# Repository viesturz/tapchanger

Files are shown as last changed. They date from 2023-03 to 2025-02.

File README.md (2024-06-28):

# Tapchanger

A nozzle Z probe + toolchanger for Voron 2.

## Features
* Off the shelf voron parts, except for bearings.
* Uses [Dragon Burner](https://github.com/chirpy2605/voron/tree/main/V0/Dragon_Burner) toolhead - can fit 6 hotends in 350 frame. [Stealthburner](https://github.com/VoronDesign/Voron-Stealthburner) and MiniStealthburner 
are an option but limited support. (Experimental version of the [Rapid Burner](https://github.com/chirpy2605/voron/tree/main/V0/Rapid_Burner) is in the works by @Marshalldog) (Experimental version for the [Xol-Toolhead](https://github.com/Armchair-Engineering/Xol-Toolhead) is in the works)
* Uses [OptoTap](https://www.google.com/search?q=optotap) probe sensor for nozzle Z probing.
* Same [rigidity](https://youtu.be/mGRXtK9F408) and probe accuracy as Tap.
* Same external printer dimensions, except for top hat.
* No servos, no wires on the shuttle, recommended to use with a Canbus toolhead board for less wires, but anything goes.

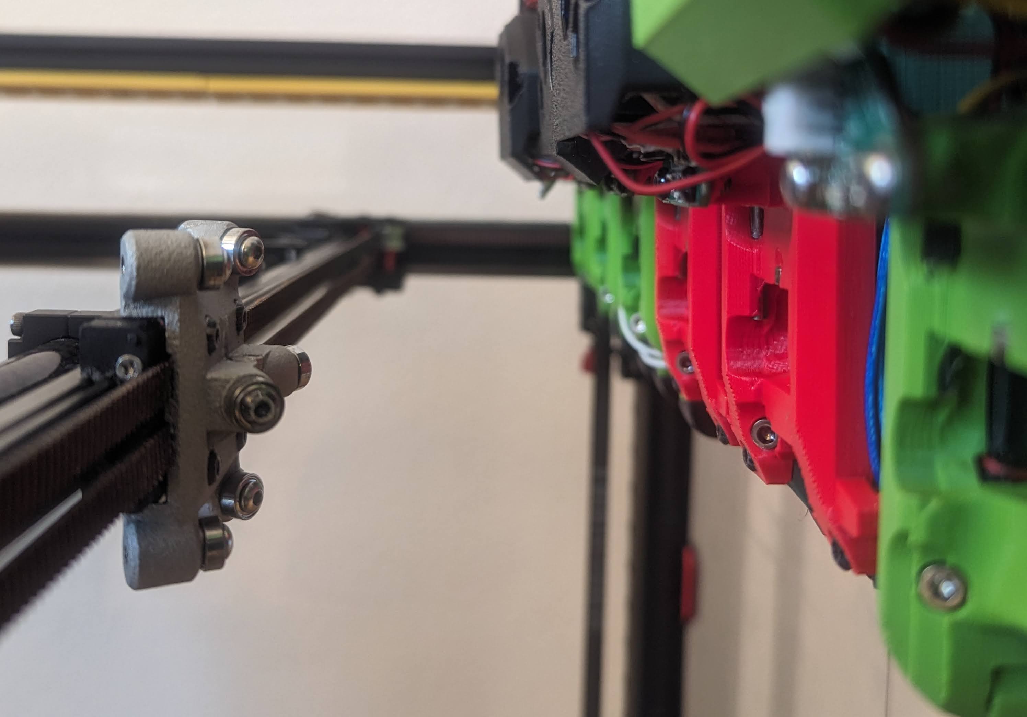
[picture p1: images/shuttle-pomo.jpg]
Shuttle

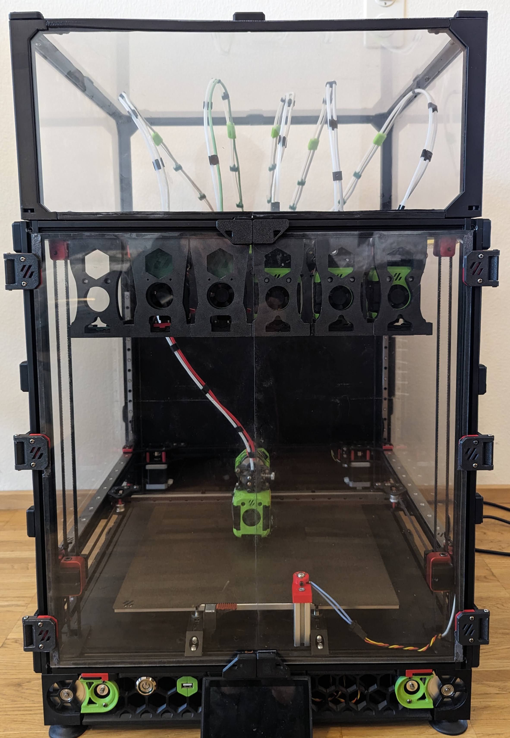
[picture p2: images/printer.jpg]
Printer
 

# Build guide

I would recommend to get a single hotend working first:

* Check the [BOM](/Tapchanger/BOM.md).
* [Print](./Print%20Guide.md) the parts.
* [Assemble](/Tapchanger/Assembly.md) it.

Multiple tools setup:
* Install [Umbilical](/Umbilical/Umbilical.md).
* Install [Docks](/Dock/Dock.md)
* Add a [TopHat](/TopHat/TopHat.md)
* Configure [Klipper](/Klipper/README.md)
* Calibrate the offsets. I'm using [this](https://github.com/viesturz/NozzleAlign)

# Community

Improvement ideas - bugs, pull requests welcome. Find me on [Voron Toolchangers Discord](https://discord.gg/xmDWrYGwVJ), or file bugs here.

See Tapchanger [youtube channel](https://www.youtube.com/playlist?list=PLqU7kX5nUJDRDw5z0NLwJ22OkV6fbjnSW).

# Credits

- Basic models from [Voron Stealthburner](https://github.com/VoronDesign/Voron-Stealthburner) and [Voron 0](https://github.com/VoronDesign/Voron-0).
- Mini SB Orbiter cowling form [mozartlovescats](https://www.printables.com/model/366337-voron-02-orbiter-20-trianglelab-chc-mini-stealthbu).
- Mini SB LGX lite cowling form [MC](https://www.printables.com/model/395933-voron-02-mini-stealthburner-remix-for-lgx-light-ex/files).
- Dragon Burner from [chirpy2605](https://github.com/chirpy2605/voron/tree/main/V0/Dragon_Burner).
- HGX gears extruder derived from [nhchiu's ProtoXtruder](https://github.com/nhchiu/VoronMods/tree/main/Extruders/ProtoXtruder)

# How does this work?

It's essentially an oversized linear rail, that supports only ~4 mm of travel. The steel rail is replaced by bearings riding on rods.

In addition, it's a kinematic mount, meaning that it's self aligning and there is no play even if the parts are not aligned precisely.

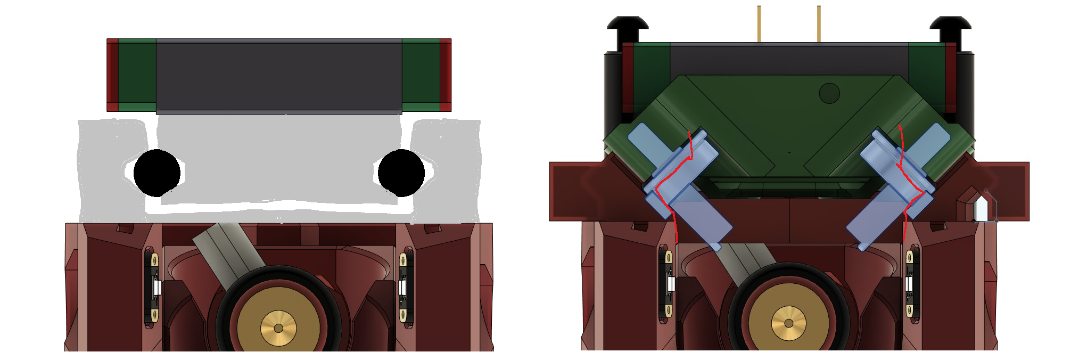
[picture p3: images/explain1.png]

Shuttle

# Revision history:

## V4.3
Dragon burner printability, ease of assembly tweaks:
* Two piece mount plate with less supports needed
* Better access to the heatset inserts
* Slightly larger sensor screw holes to better work with polycarbonate
* Will need to reprint the cowling as well, slight changes there

## V4.2
Small tweaks across the board:
* Dragon toolhead mount plate 1mm thicker - no interferance with fans and 8mm tensioning screws do not stick out
* Fix shuttle mounting plate misalignment, thanks [vikwin](https://github.com/vikwin) for spotting
* Alternative version for the PFTE tube holder at the side
* Dock for RapidBurner
* Extras
  * Better ventilated EBB36 shield 
  * Improved strain relief for HGX + DragonBurner
  * More Stepper gear distance adjustability for HGX + DragonBurner.

Dragon burner toolhead exploded view: 

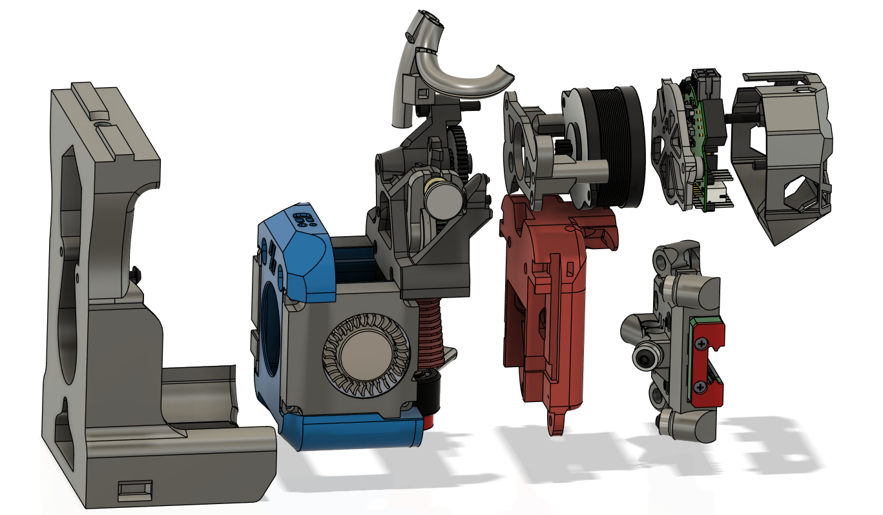
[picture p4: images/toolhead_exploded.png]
Exploded


## V4.1
HGX gears + Dragon + EBB36 [optimized toolhead](/Tapchanger/STL/Toolheads/DragonBurner/HGX%20Gears/):

* 17 mm shorter filament path
* 17 grams lighter than stock, only 2 screws
* Integrated harness strain relief
* Integrated EBB36 mount & shield
* Bambu & Revo adapters only for now
* There will be some supports to remove.

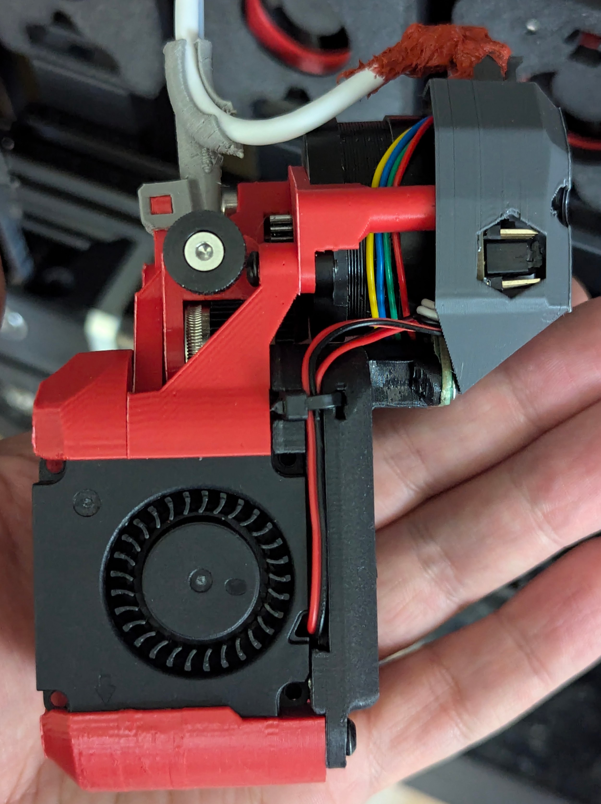
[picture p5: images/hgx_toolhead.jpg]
HGX gears toolhead


## V4.0
[Liftbar dock](/Dock/Liftbar/Liftbar.md)

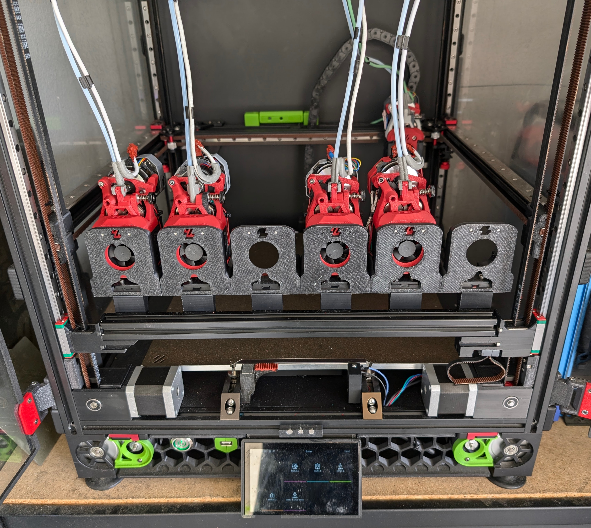
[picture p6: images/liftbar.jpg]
Liftbar


Other minor DragonBurner changes:
* More clearance around the hookon slot.
* More room around the cooling fans, to avoid cracking the cowling when tightening the bottom screws.
* More sturdy dock.

## V3.2
Introduces support for the Experimental Rapid Burner Toolhead by @Marshalldog.

## V3.1
End of year update, lots of small printability, clearance, etc updates. 
This is a stable version.

* Migrated to Dragon V8 hotend.
* More clearance around the OptoTap sensor.
* Tuning of the tension screw angles to minimize the docking resistance.
* More clearance for big block hotends.
* Hook-on dock is now the recommended for DragonBurner.

## V3.0

Further improvements to DragonBurner toolhead and dock.
The screw head locking mechanism is back.
Configuration updated, with better dock pathing.

The Dragon Burner toolhead is now the default. Let me know if you would like to see backports.

## V2.9

Improved DragonBurner toolhead and dock, adding bottom mounting screws for better stability.
Needs the modified cowling now.

## V2.8

# Added Tophat and Ubmilical, it's now a Printer!

Printer 

## V2.5

* Added top mounted dock. see updated Dock folder.
* Slight tweaks square rods mounting plate for easier fit.

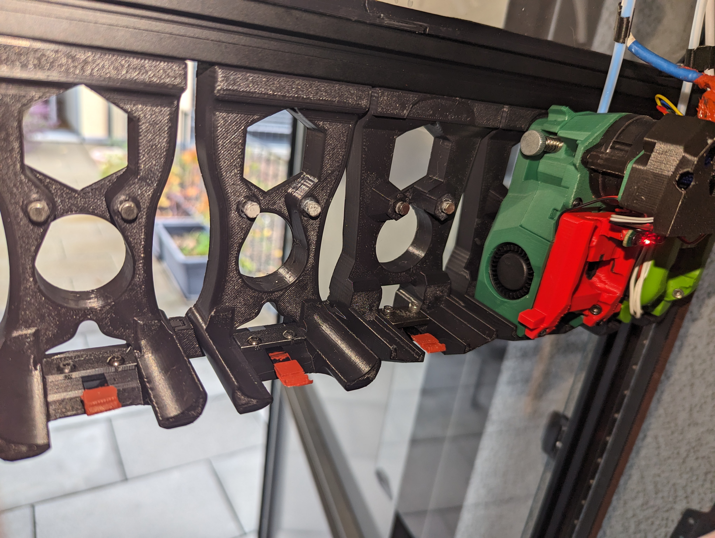
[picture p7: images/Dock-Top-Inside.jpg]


## V2.3 - Nozzle pads upgraded to springsteel ones, no more melting.

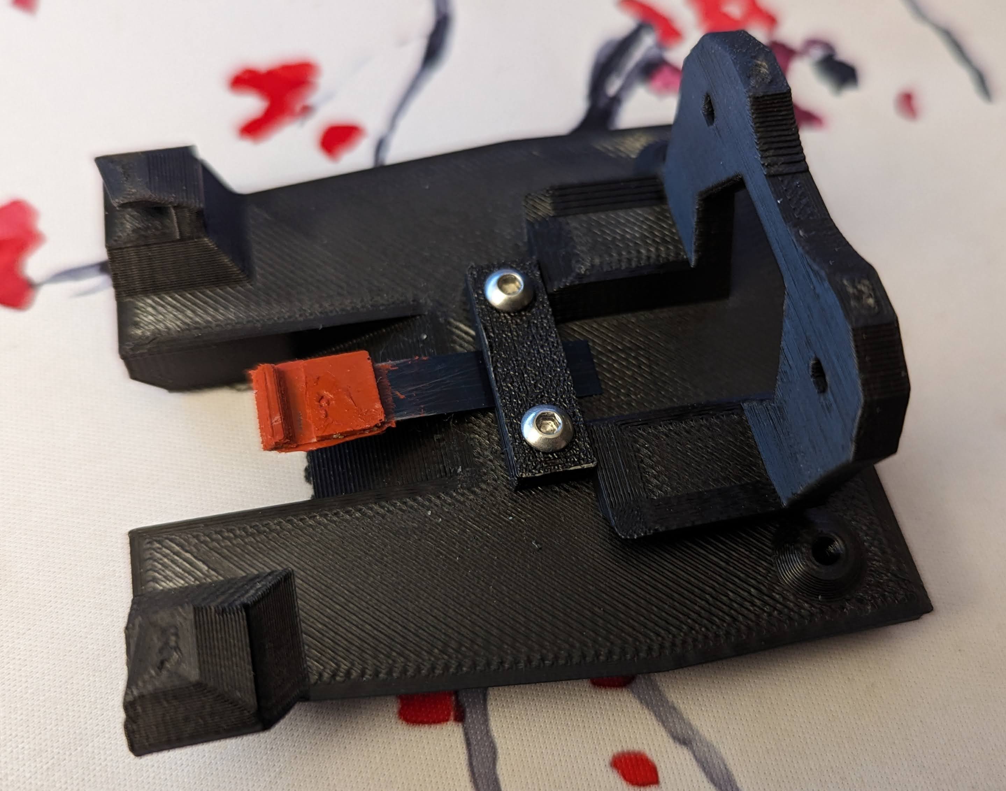
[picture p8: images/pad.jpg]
Pads


## V2.2 - Square rods version added.

Option to use square rods for better contact surface for the bearings.  Shares the shuttle and bearings with rods.

There are now total of 3 versions:
 - Plates - bigger bearings, more work to make the plates and assemble. The rolling surface is not great. Very rigid.
 - Rods - smaller bearings, easiest to assemble, but more flex.
 - Square rods - middle ground between plates and rods, the rigidity testing was done with this.

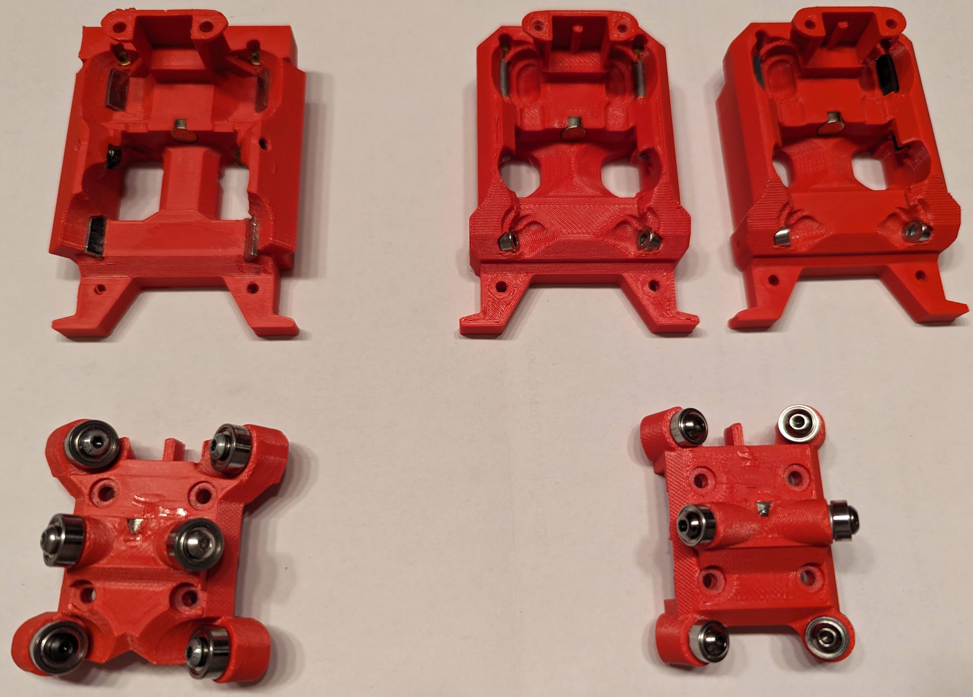
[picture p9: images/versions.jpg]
Versions


## V2.1 - Rods fixes.

Various fixes to refine the rods version. Ready for general testing.

## V2 - Rods version added.

A new experimental version using 3mm rods. See -rods files. Shuttle and mount plates changed, the rest is same.

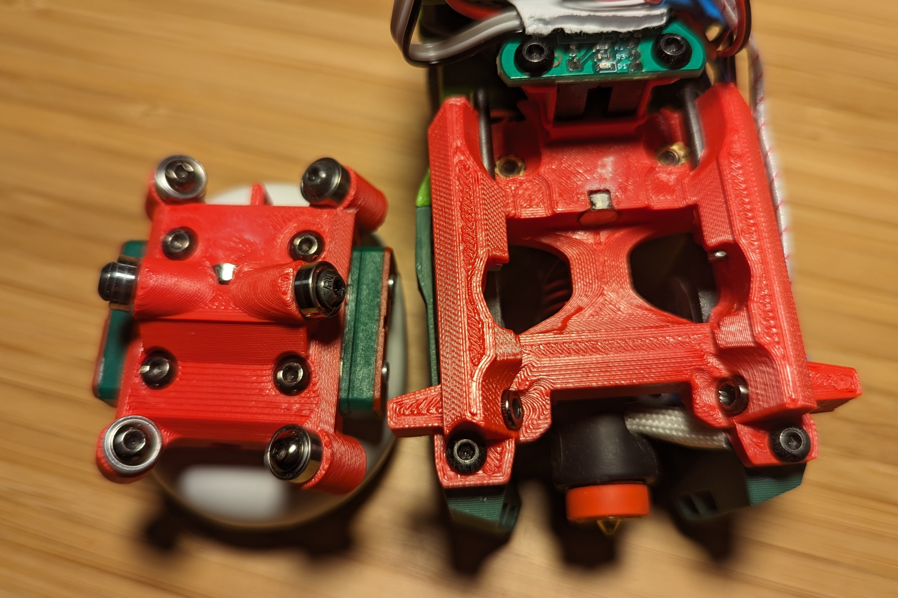
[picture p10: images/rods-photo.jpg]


- Easier to assemble
- Tension adjustment screws easily available
- Runs smoother
- Using smaller 3x8x3 bearings - saves 5 grams and even more rigid.
- Even load distribution between the bearings by adjusting the angles to 26 and 64 degrees.

## V1.1 - Verified and cleaned up.

- Minor model tweaks for better fit and printability.

## V1 - This should work

- Redesigned and optimized - not compatible with V0
- Significanly more rigid
- Supports both Mini and full size Stealthburner

## V0 - Initial drop
 
 - It can print and looks reasonably rigid
 - ~10 Tool chnages so far
 - Initial dock, that looks okay for the job

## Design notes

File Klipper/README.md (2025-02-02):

# Klipper setup

## Overview

TapChanger is primarily a hardware project. The config here is just the setup I'm using.
Which should be a reasonable starting point.

I'm working to upstream the changes in klipper where reasonable.

## Installing

- Install [toolchanger extension](https://github.com/viesturz/klipper-toolchanger/).
- Use the [config examples](https://github.com/viesturz/klipper-toolchanger/tree/main/examples) to setup your Klipper config.

## Prusa slicer config

I'm using the following custom Gcode.

**Start Gcode** - all must be a single line
```
PRINT_START  TOOL_TEMP={first_layer_temperature[initial_tool]} {if is_extruder_used[0]}T0_TEMP={first_layer_temperature[0]}{endif} {if is_extruder_used[1]}T1_TEMP={first_layer_temperature[1]}{endif} {if is_extruder_used[2]}T2_TEMP={first_layer_temperature[2]}{endif} {if is_extruder_used[3]}T3_TEMP={first_layer_temperature[3]}{endif} {if is_extruder_used[4]}T4_TEMP={first_layer_temperature[4]}{endif} {if is_extruder_used[5]}T5_TEMP={first_layer_temperature[5]}{endif}  BED_TEMP=[first_layer_bed_temperature] TOOL=[initial_tool]
```

**Tool change Gcode**
```
M104 S{temperature[next_extruder]} T[next_extruder] ; set new tool temperature so it can start heating while changing
```

## Optional - Z homing with any toolhead.

The included config has a rather elaborate setup that allows Z homing with any toolhaed. This avoids the need to ensure that toolhead 0 is mounted before homing.

The tool changing needs reasonably repeatable gantry Z position, since Tap homes to nozzle possition, it will be different for each toolhead.

So this is a bit more complicated than yor typical setup:

  - Printer Z=0 - is tool independant, all toolchange moves happen in this space.
  - Tool probe trigger Z offset - distance betwen nozzle touching the bed and probe triggering - is tool specific, but nozzle independant. Specified in tool_probe.z_offset.
  - Tool Z offset - is tool and nozzle specific. Specified in tool.offset.

When **homing** the Z=0 is determined from probe tigger location - probe trigger offset - tool Z offset.
For Tool 0 that is the same as normal Tap homing. For other tools the extra tool offset is substracted.
Klipper unfortinately assumes that the Z=0 is a fixed distance from the endstop trigger location, so there are some tricks in homing.cfg to adjust this in post.

When **printing**, the Gcode offset is = tool Z offset.

When **changing tools**, Gcode offset = 0.

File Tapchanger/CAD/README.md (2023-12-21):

The holes are not present in the CAD. Please use the provided hole models to cut either square or round holes.

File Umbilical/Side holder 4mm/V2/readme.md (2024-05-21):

Side PTFE tube holder with individual locking nuts.

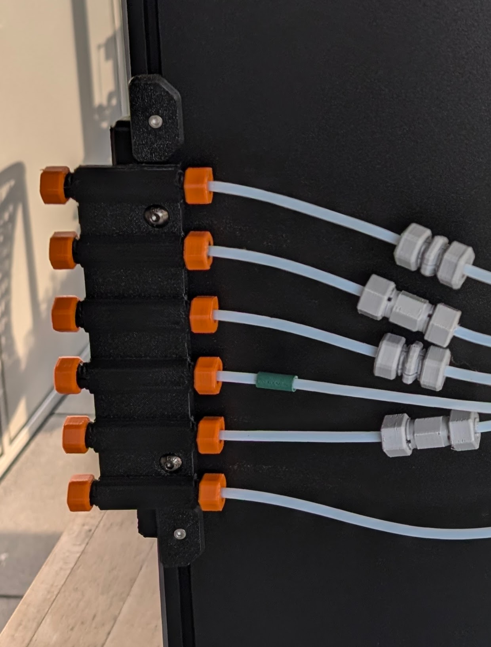
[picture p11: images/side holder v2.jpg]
Preview


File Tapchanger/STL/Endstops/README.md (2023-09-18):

# Endstops

I recommend sensorless XY. 

# X endstop on Y axis

Use `HallSensor.stl` - it is a copy of Tap switch/magnet mount adapted for the shuttle.

# X endstop on Gantry

Very prototypy, moves the X endstop to the gantry, removing wiring to Y axis.

Use `X Endstop Lever.stl`.

It's very specific for Chaoticlabs motor mounts and some Y endstop PCB I had laying around.

Preview
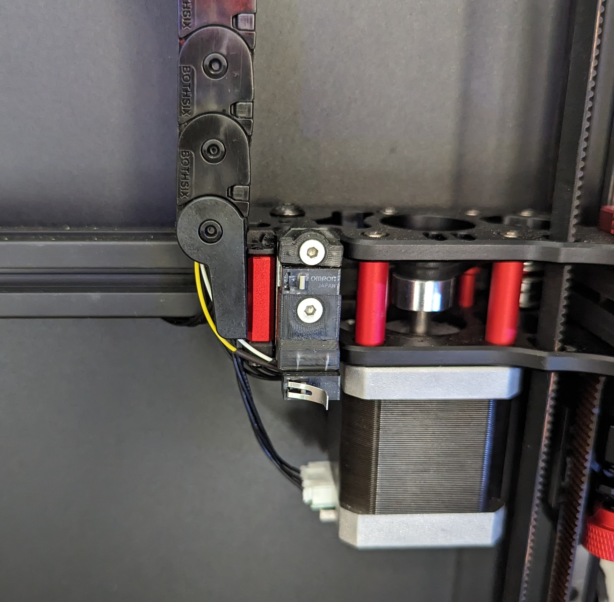
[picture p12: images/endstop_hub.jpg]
Preview


Ping me if you happen to make a better solution.

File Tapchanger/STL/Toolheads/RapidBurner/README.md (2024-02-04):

### Rapid Burner Toolhead implementation is experimental and currently under testing by @Marshalldog.
### Use the parts from the Dragon Burner (except the cowl).
# This is EXPERIMENTAL. If you have issues, please post them on the tapchanger discord ASAP!

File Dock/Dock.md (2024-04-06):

# The dock

The dock comes in 3 versions - cross beam mounted, top mounted or on rails.

| Top mounted  | Cross beam | Liftbar | 
| --- | --- |  --- |
| * Can be installed in existing frame<br> * Good clearance |  * Supports Full sized Stealthburner <br>* Extra docking latch | * Complex to build <br> * Best clearance <br>* Slightly faster changes<br>* Can install on Trident |
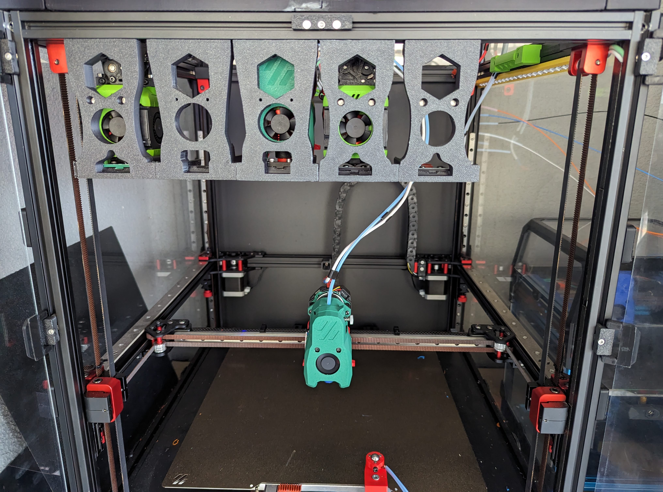
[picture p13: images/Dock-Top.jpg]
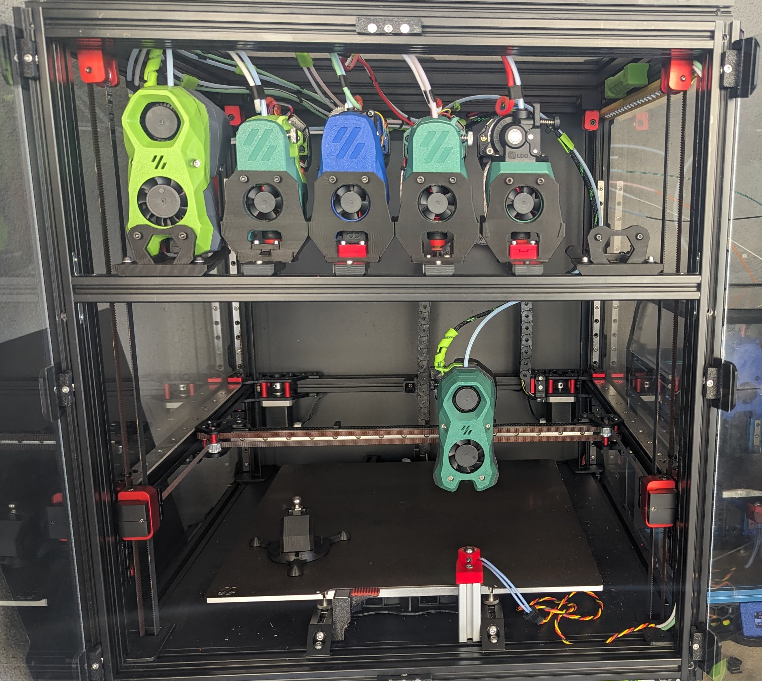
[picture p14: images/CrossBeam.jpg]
|  |   |  Preview  | 
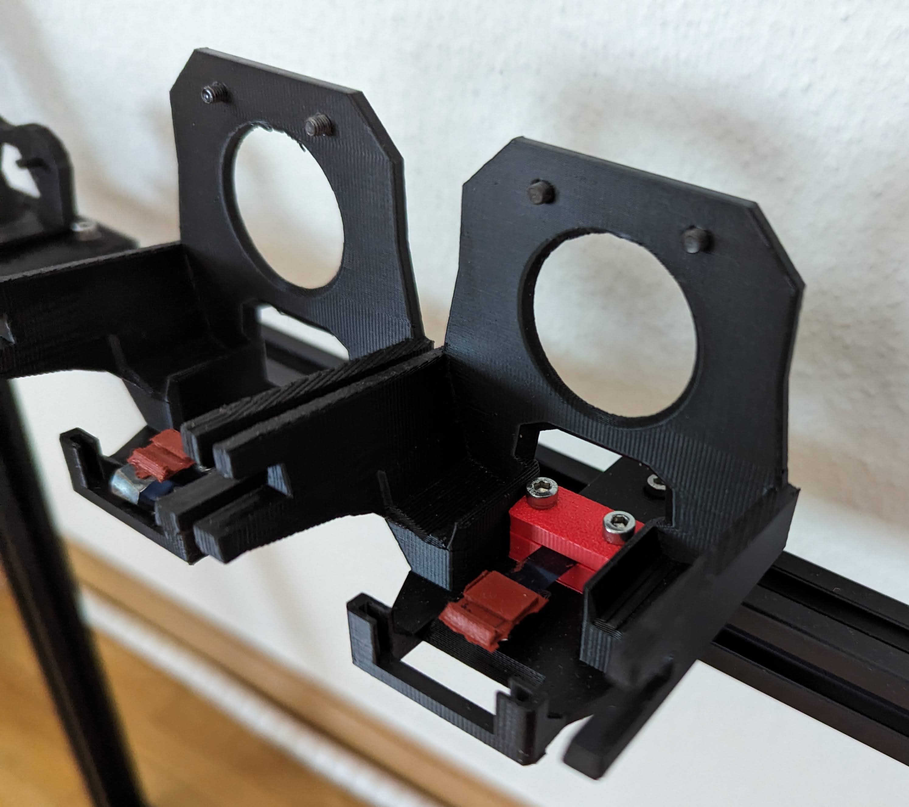
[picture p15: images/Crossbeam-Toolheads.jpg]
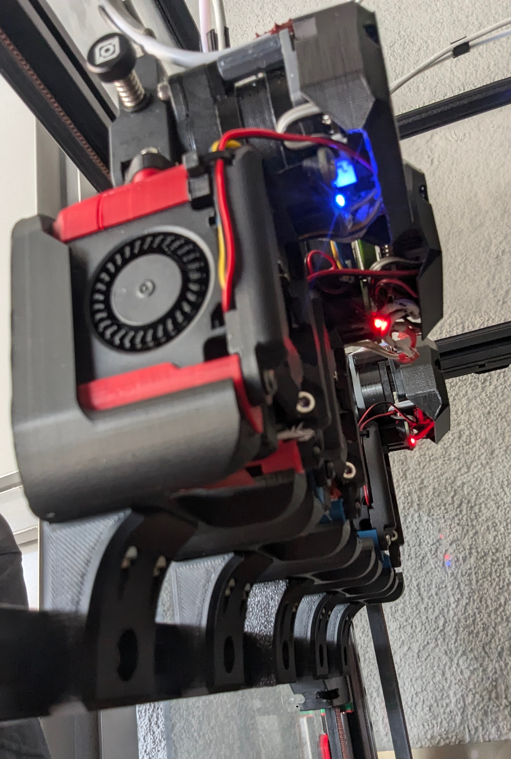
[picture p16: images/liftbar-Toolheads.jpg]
| Preview |  |  |

# Liftbar dock 

See [Liftbar instructions](./Liftbar/Liftbar.md)

# Other docks BOM

 - High temp silicone for the nozzle pad
 - 35 mm of 7x0.1mm springsteel, salvageable from 1m tape measure.  
 - some M3 screws and heatset inserts
 - *retnetion hardware* - see below

# Toolhead retention

There are 2 versions of retentiom mechanism, this will likely converge as I get more relibility data

## Screw head hook

Dragon burner uses this method.
The toolhead hooks on to the M3 scew heads. Just need 2x m3x10 butthonhead screws.

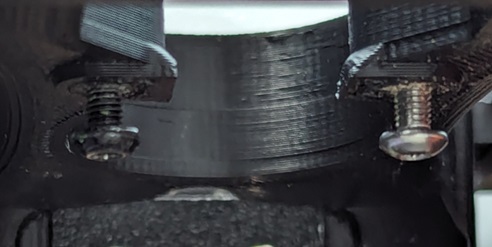
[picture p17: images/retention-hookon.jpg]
Cross beam retention


## Bottom pin + magnet to toolhead screws.

Stealthburner and mini stelathburner on cross beam uses this approach.
It relies on a bottom pin as the main retention mechanism and the magnet is just to prevent it rattling around.

You will need:
  - 2x 5x2mm round magnets
  - 2x m3 x 10 steeel screws in the dock - steel (magnetic)
  - the screws in toolhead also need to be seel to stick to the magnets

Drop the magnets on the screw heads in the toolhead. They will stay there on their own, no glue required.

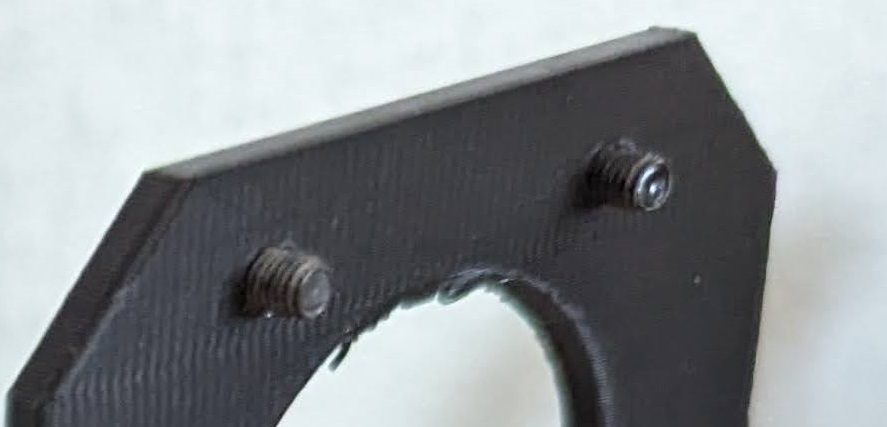
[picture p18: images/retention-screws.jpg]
Cross beam retention


# Cross Beam Frame BOM

Essentially you need to build this. The exact dimensions depend on your printer size.

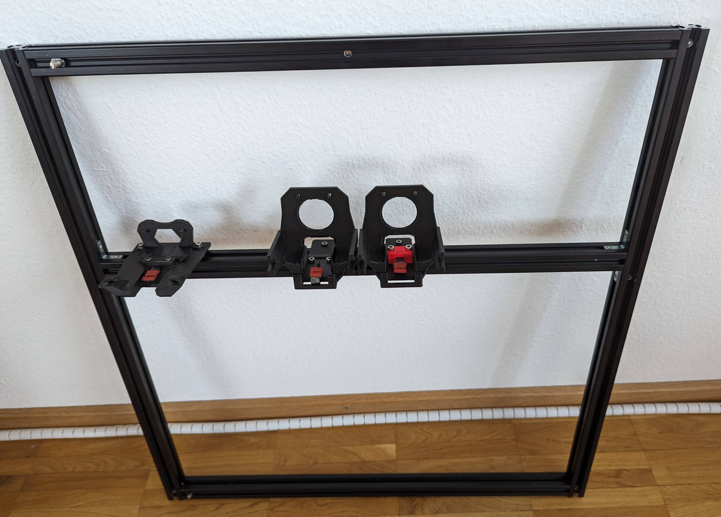
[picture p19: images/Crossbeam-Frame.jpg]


# Nozzle pad

Print the nozzle pad mold. Put on some mold release, just rubbing with a birthday candle works well. 

Cut a 35mm piece of springsteel and mold the silicone pad on one end.
The mount is designed to accomodate fror the springteel curve, place it so that it curves downwards.

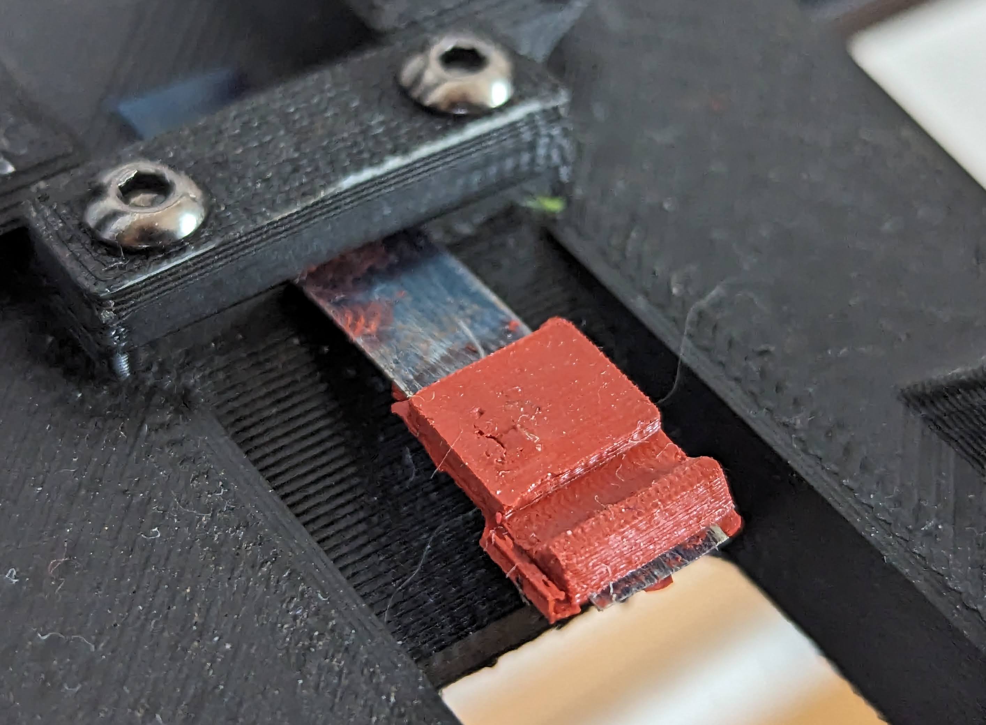
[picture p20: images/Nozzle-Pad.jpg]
Pad


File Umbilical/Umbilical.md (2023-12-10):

# Umbilical

The wiring system from the main board to all the toolheads.

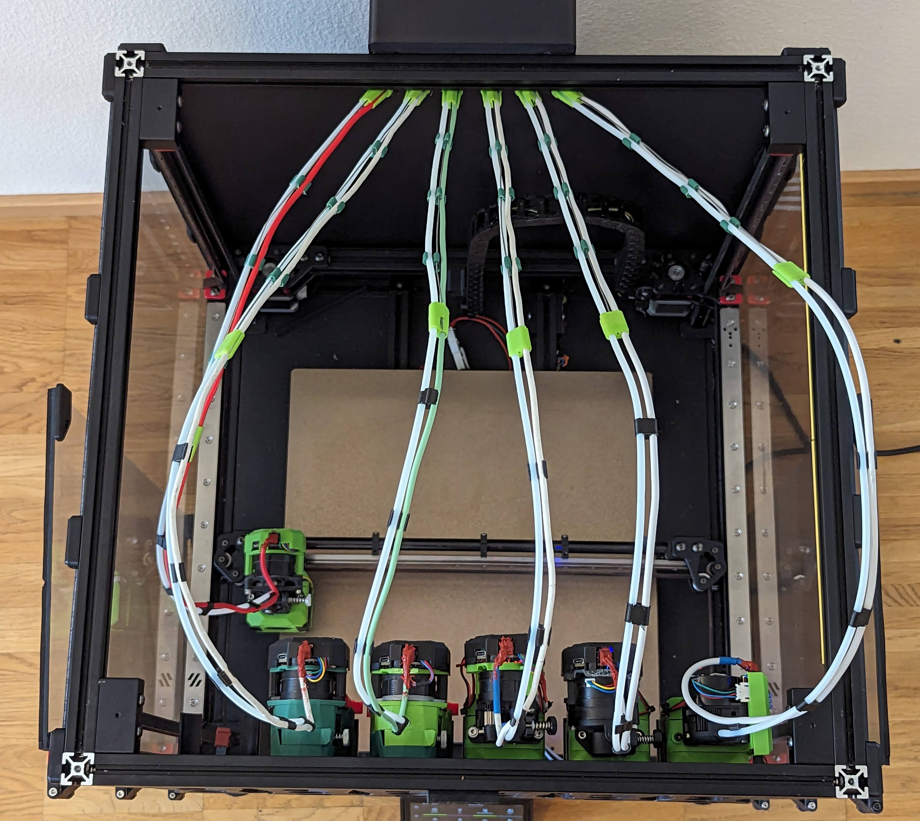
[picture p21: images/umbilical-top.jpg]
Preview


# BOM (per toolhead)

All lengths are for a 350mm bed build. Shorten accordingly for smaller sizes.

* Some TPU filament, I'm using 82a hardness.
* 34cm 1mm piano steel wire
* 1m USB cable, capable of 5amps
* silicone (high temp or normal)
* 130cm PTFE tube 4mm OD, 3mm ID
* Some m3 and m5 scews and heat set inserts

# Assembly

## Backing plate

Mount the back plate at the back of the rail, it replaces the air filter.
Route the canbus wires and 24v to it. They fit will in the extrusion slot. Remember to use appropraite gauge, for all 6 toolheads it can draw 20+ amps, and more if you go for Rapido for some reason.

I'm currently using Wagos to connect all the wires, but see the electronics folder for a custom PCB board.

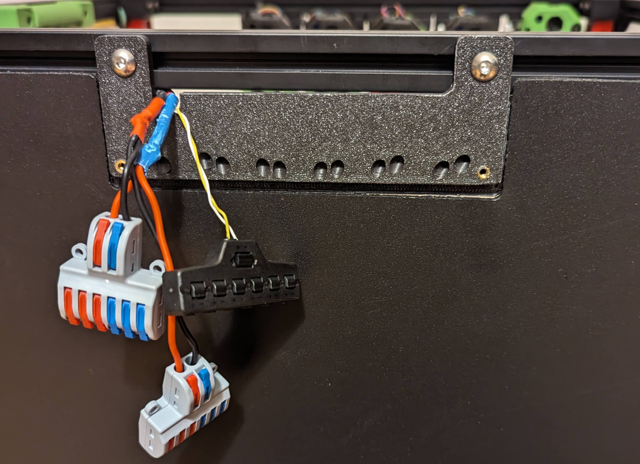
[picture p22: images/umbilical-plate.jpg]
Plate


## Prep the USB cable

Cut both connectors off, and solder/crimp on the hotend board connector. Then **fill it up with silicone**, this is high vibration connection, I had constant connection issues without this. 

Leave the other end alone for now, it will make it easier to thread through the backing plate.

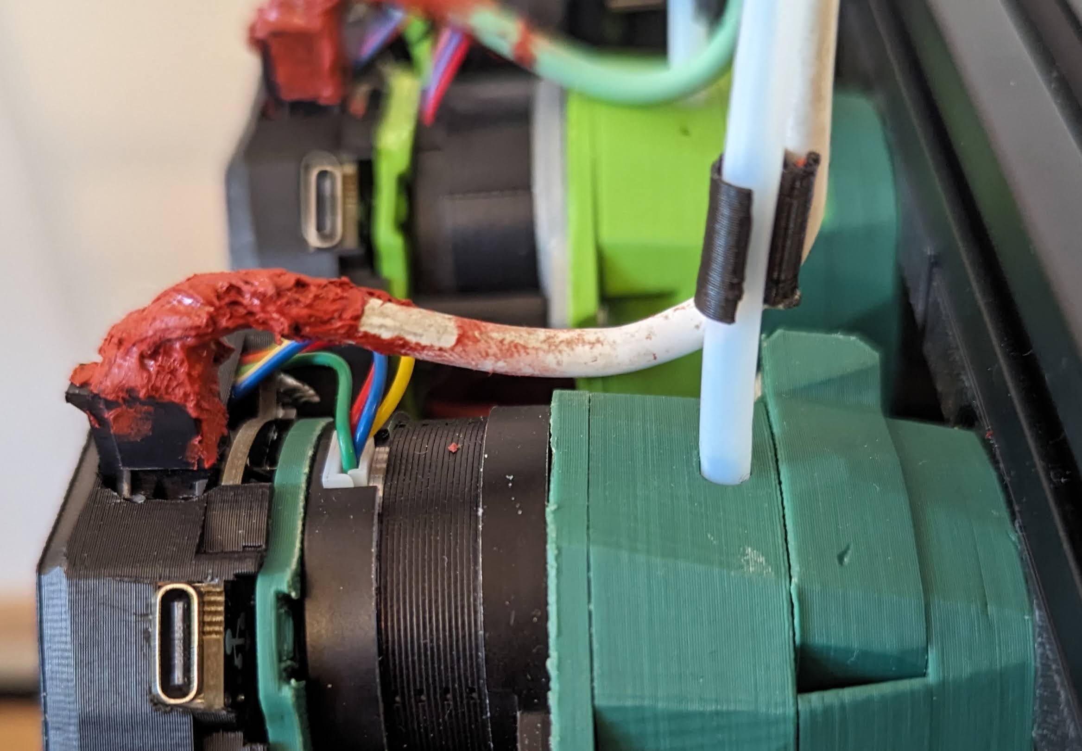
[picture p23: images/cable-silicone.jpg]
Toolhead connector


## Prep the piano wire

Cut the piano wire to length, straighten it out (holding with pliers and lightly bending works well). And fold a square hook at one end, you will need that to secure in the TPU plug.

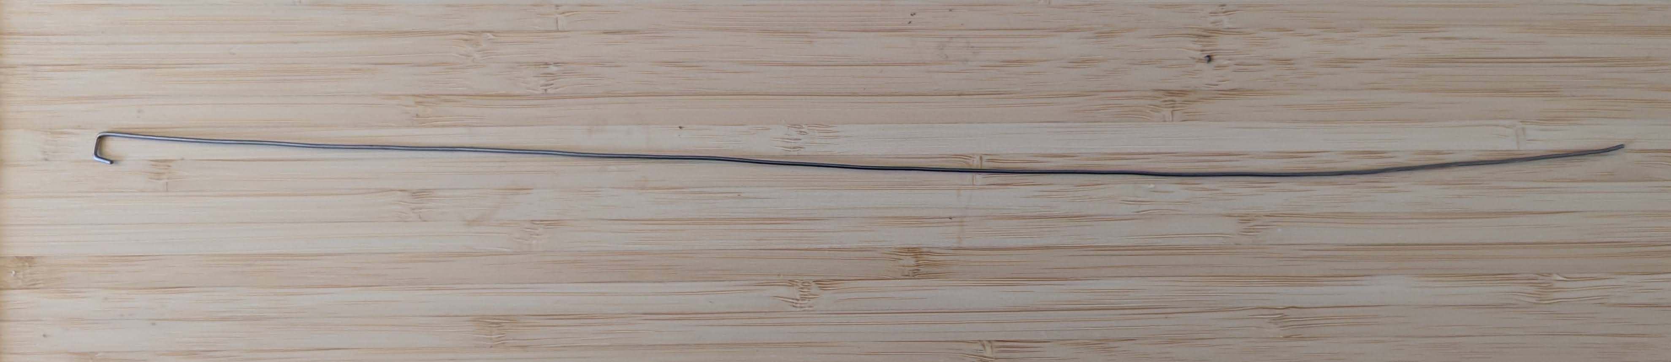
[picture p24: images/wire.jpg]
Wire


## Assemble the umbilical

Attach the both ends to the wire and put 3 wire clips in the middle. **Mind the orientation** - USB cable goes on the right and PFTE tube on the left side.
Both the clips and the hub are designed with tube on the left. The hole sizes are different so it should be obvious that something is off.

Leave around 40 cm of the tube and 45 cm of the usb cable from end of wire to the toolhead. You will be able to adjust it later.

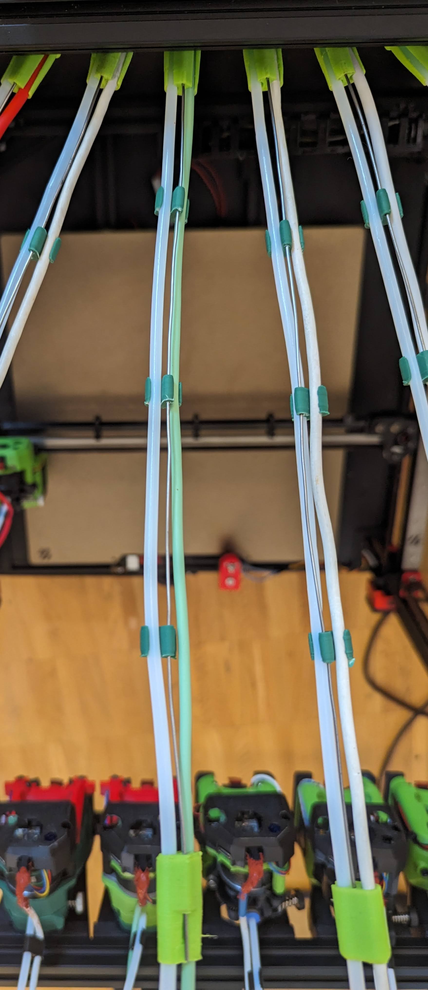
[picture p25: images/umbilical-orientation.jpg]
Umbilical


## Install

Plug the umbilical in a slot, it's a tight fit but should go in with some pressure applied. Attach the toolead.

Now move the toolhead around the print area, make sure the cable is long enough to reach every corner. Adjust the length as needed.

It should be roughly like this:

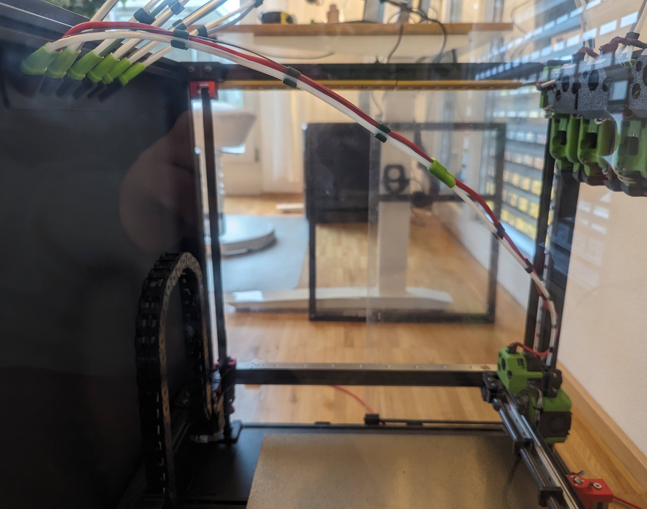
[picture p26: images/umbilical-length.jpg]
Umbilical length


## Connecting

Now you can cut the USB cables to length, strip and connect them.

See [Canbus](./canbus_wiring.md) on how to wire it all together.

**Before powering on**, verify there are no shorts and the Canbus lines have 60 Ohm between them.

## Filament routing 

Attach the tube holder to the side and route all the tubes through.
Mine where cut too short, so I had to improvise.

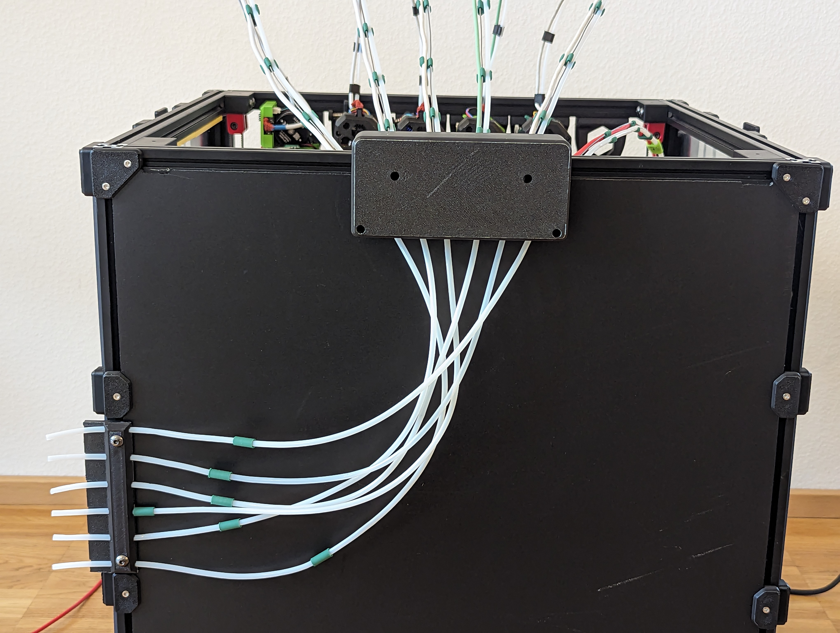
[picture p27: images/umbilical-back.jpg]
Umbilical back


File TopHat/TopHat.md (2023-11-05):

# Tophat to encose the umbilicals.

Adds a 20cm extra clearance for umbilicals. Reuses the top plate.

Theese are some big pieces to print from ABS:

- the **beams are 0.5% longer** and have bigger screw holes and support 0.5-1.5% shrinkage
- add mouse ears or there is high chance the beams will peel off

It just sits on top of the frame with alignment pins dropping down into the extrusion slots

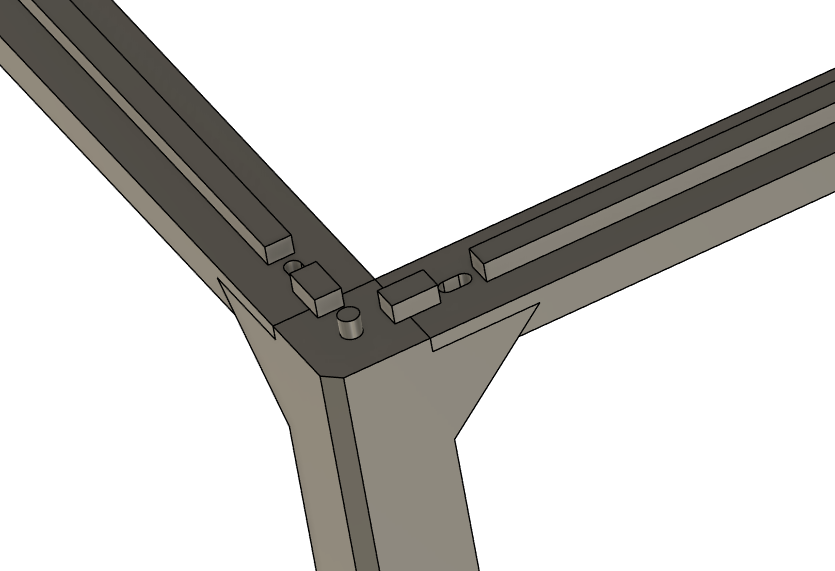
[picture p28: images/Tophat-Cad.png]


# BOM

* ~600g of filament
* 4x 200x477 acrylic plates, 3mm thickness
* 1mm sponge tape
* some M3 screws and heat set inserts

# Preview

Of an older version.
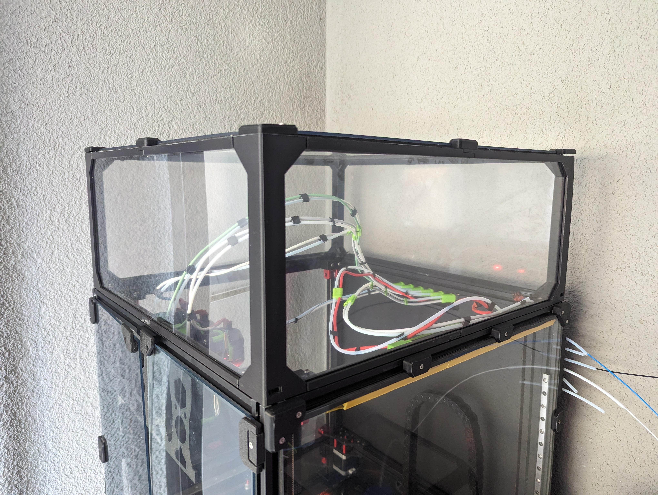
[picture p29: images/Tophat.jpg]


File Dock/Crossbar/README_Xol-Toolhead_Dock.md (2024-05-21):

# Tapchanger-Rods Xol-Toolhead (Experimental)
by [MikeYankeeOscarBeta](https://github.com/MikeYankeeOscarBeta/tapchanger) (VoronDesign Discord: #MikeyMike V2.5796, Voron Toolchangers Discord: MikeyMike - Github: [MikeYankeeOscarBeta](https://github.com/MikeYankeeOscarBeta/tapchanger))

### This is EXPERIMENTAL If you have issues, please post them on the tapchanger discord ASAP!

## Description
Tapchanger parts compatible with Xol-Toolhead (Experimental)

Based on Tapchanger StealthBurner Parts.

For crossbar (horizontal 2020 aluminium extrusion in front of printer) only!

Designed to be compatible with all Xol-Toolhead versions as of 2024-01-19.
(However only Revo Voron and Rapido 2 UHF has been tested)

#### NB! Tapchanger-Rods Xol-Toolhead dock has it's own docking tool-path. Remember to change to 'rods_xol' in your toolhead config.
In case you don't already have it from the tapchanger example config toolchanger.cfg , here's the docking tool-path:
```
params_rods_xol_path: [{'y':59, 'z':17.5},{'y':5, 'z':17.5},{'y':5, 'z':0.2},{'y':0.5, 'z':0.1},{'z':0, 'y':0, 'f':0.5},{'z':-5, 'y':0},{'z':-6, 'y':3},{'z':-8, 'y':7},{'z':-10, 'y':16}]
```

#### NB! only compatible with tapchanger rods version as of 2024-01-19

Example:
```
[tool T0]
tool_number: 0
extruder: extruder
params_type = 'rods_xol'
fan: multi_fan T0_partfan
gcode_x_offset: 0
gcode_y_offset: 0
gcode_z_offset: 0
```

## BOM:
| Part | Amount | Description |
|---|---|---|
| 6x3 magnets | 4 | N35 to N52 (N52 recommended) |
| springsteel plate | 1 | max 10mm wide, max 1mm thick, with M4 hole (I used blades from a [feeler gauge](https://www.biltema.no/en-no/car---mc/car-tools/engine-tools/spark-plug-tools/feeler-gauge-mminches-2000028588) ) |
| M4 screw | 1 | Maximum 6.3mm wide screw head |
| M3x14mm BHCS or SHCS screw  | 2 | Any M3 screw will work |
| M3 T-slot nut | 2 | Any M3 2020 T-Slot Nut will work (recommend springnuts) |

## Assembly
- Print
    - dock
    - maglock faceplate
    - tapchanger-rods xol-base
    - tapchanger-rods shuttle (if you haven't already)
- Push and glue in magnets
- Insert springsteel plate into slot in the Dock
- Cut and bend springsteel plate to fit your toolhead
- (optional) apply/mold silicone to the springsteel plate
- Fix the springsteel plate in place with the m4 screw
- Screw it onto the 2020 aluminium extrusion

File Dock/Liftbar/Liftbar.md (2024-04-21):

# Liftbar dock

A motorized crossbar - compatible with Trident and V2.

For up to 3 toolheads (2 docked), a single motor is sufficient. For more, I recommend two motors.

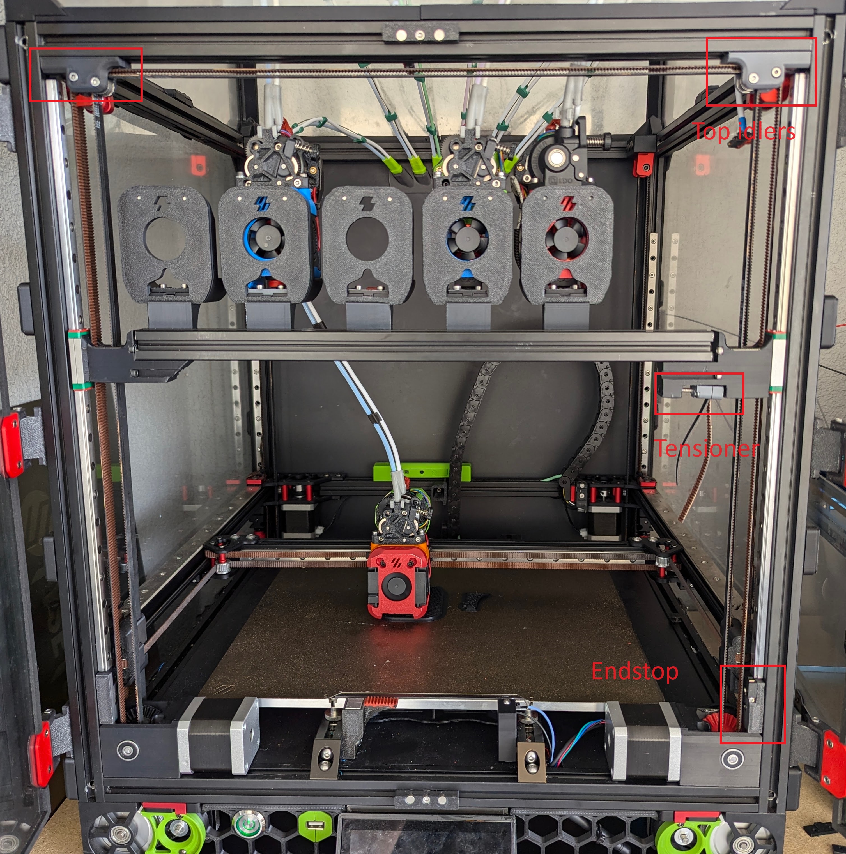
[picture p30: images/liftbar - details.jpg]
Details image


## BOM
2020 Extrusion:
 -  279mm long for 250mm build
 -  329mm long for 300mm build
 -  379mm long for 350mm build

XY Idlers:
 - 2x 20mm 5mm shaft
 - 4x heatset inserts
 - 4x 8mm m3 screw
 - existing pulleys

Common:
- Omron d2f endstop switch
- ~4m 6mm GT2 belt (for 350 size)
- m3 bolts, heatset inserts, nuts
- 8x 8mm m4 bolts, t-nuts
- 8x F623RS flanged bearings (voron 0 spec)

Voron 2.4:
- 2x MGN9H rails, same length as your Z rails

Voron Trident: 
- 2x  MGN9H rails, 210mm+

For Single motor:
- nema 17 motor
- 36mm 5mm shaft
- 2x 625 bearing (voron 2 spec)
- 20T GT2 idler
- 20T GT2 pulley
- 2x 5x1mm washers

For dual motor:
- 2x nema 17 motor
- 2x 36mm 5mm shaft
- 4x 625 bearing (voron 2 spec)
- 2x 20T GT2 pulley
- 4x 5x1mm washers

## Assembly

* Assemble and replace the the XY idlers
* Install the Top idlers
* Install the linear rails, make sure they clear the XY idlers
* Install endstop
* Assemble and connect the gearboxes
* Assemble the gantry
* Install the belt
* Adjust the belt so that the gantry is ~horizontal
* Tension the belt
* Test the lifbar movement

Work in progress...

### Gearbox

The assembly sequence is a bit tricky.

* First mount the gears - small on the stepper axis and large on the pulley. Use the grubscrews in reverse to tighten the large gear. The small gear is just friction fit.
* Then install the m3 screws for the motor, do not mount the motor yet.
* Then press fit in the rear bearing, this needs quite some force, use a rod or hex wrench through the front hole to push it in.
* Install the Left side M4 screw, but *not* the right one.
* Install the big gear, this is a bit tricky:
  * Push in the shaft through the bearing from back, have it extend 1mm inside.
  * Place the washer on the shaft
  * Push the gear assembly down from above, it's a right fit, but should go in without much force.
  * Push the shaft all the way through
  * Add the second washer and bearing.
* Install the motor, test if the gears mesh smoothly
* Install the remaing 2 M4 screws.

Cross cut vs Trident leadscrew:

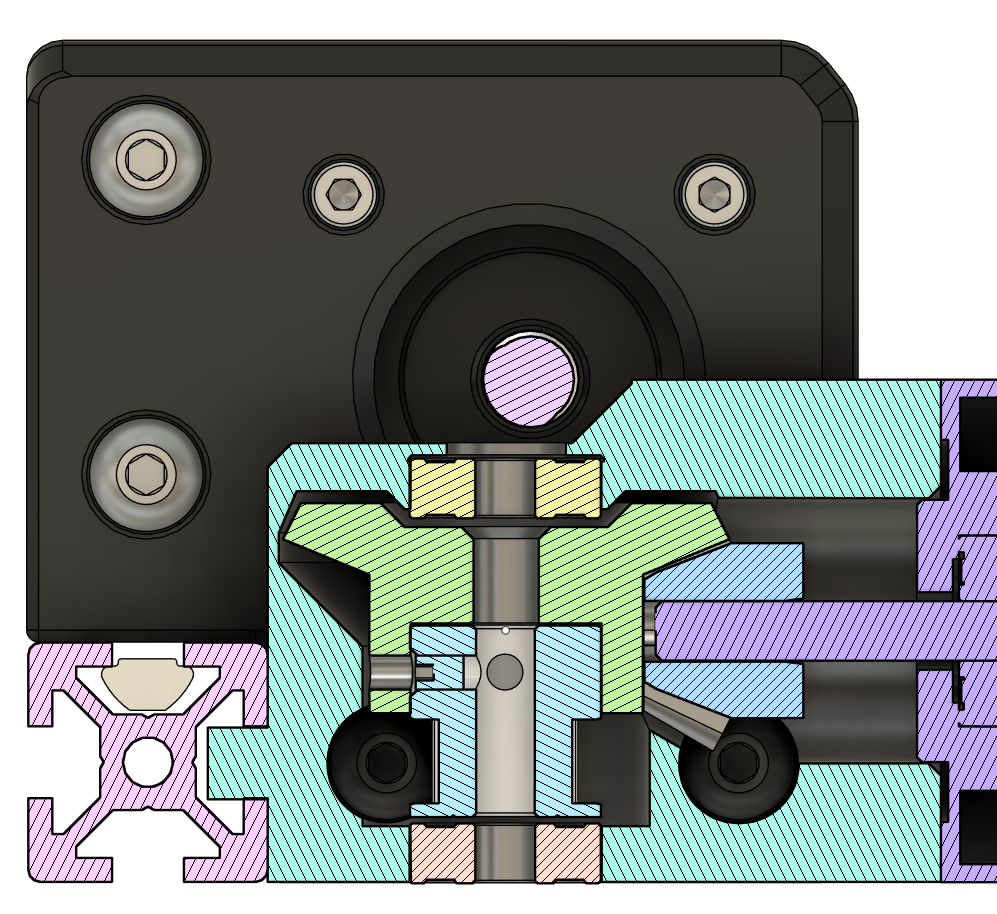
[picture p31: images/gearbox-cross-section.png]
Gearbox 0


Top down, test fitting the Motor, remove the motor to install the large gear.
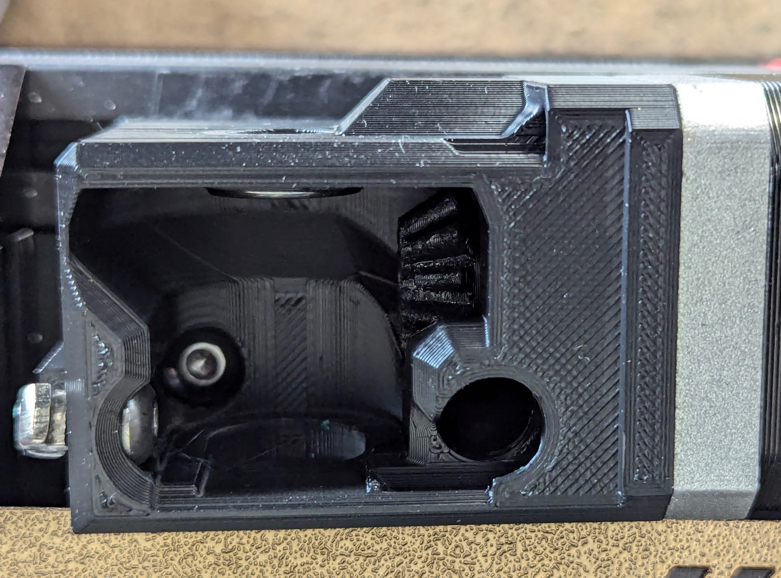
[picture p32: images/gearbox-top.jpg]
Gearbox 1


Finished, ready to be mounted:

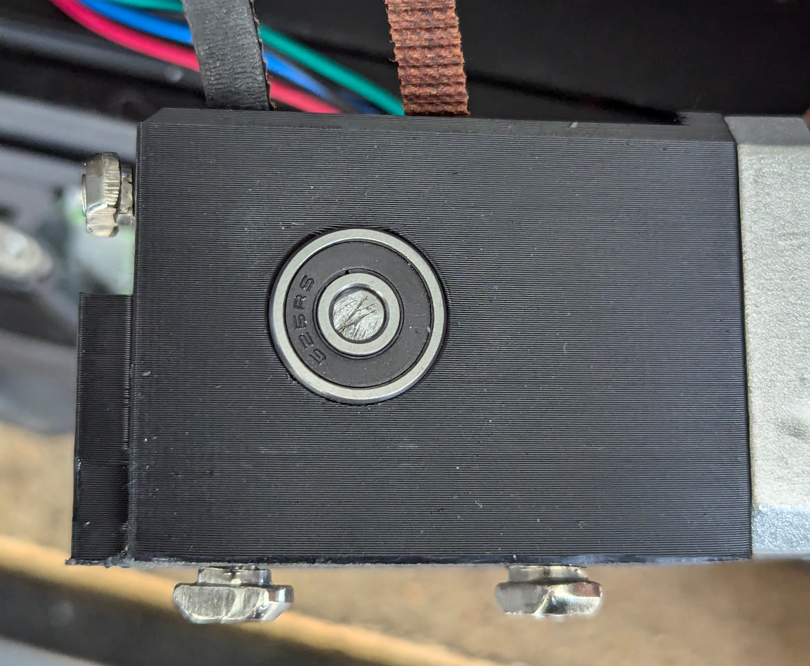
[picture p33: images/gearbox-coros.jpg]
Gearbox 1


### Docks
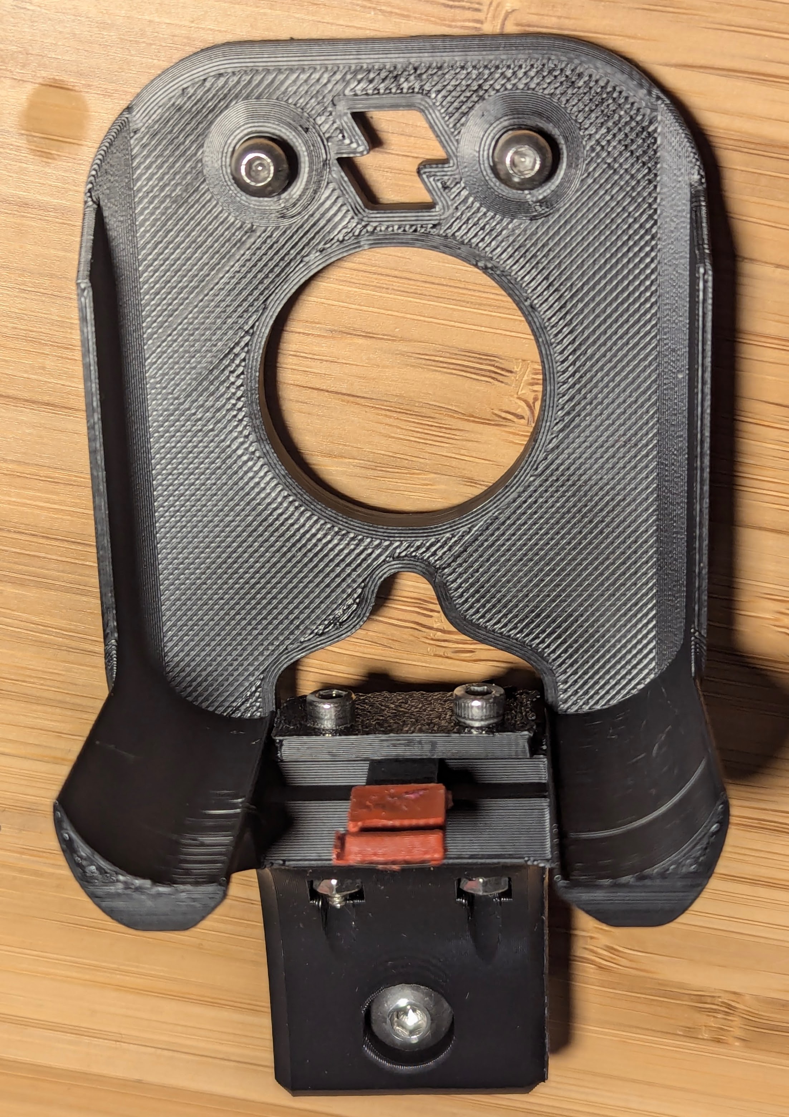
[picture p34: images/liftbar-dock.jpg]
Gearbox


## Configuration
See toolchanger-lifbar.cfg in Klipper folder.

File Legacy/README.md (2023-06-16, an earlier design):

# TapChanger - a toolchanger for Voron 2
A toolchanger system For [Voron 2](https://github.com/VoronDesign/Voron-2) based on the [Tap](https://github.com/VoronDesign/Voron-Tap) bed probe.

This is independant effort, not affiliated with the Voron team. Use at your own risk.

## Features
* Drop in compatibe with [Stealthburner](https://github.com/VoronDesign/Voron-Stealthburner) hotends.
* Adaptable from [Tap](https://github.com/VoronDesign/Voron-Tap) with mostly just printed parts.
* Same rigidity and probe accuracy as regular Tap.
* Mostly staying within the same external printer dimensions.
* No servos, no wires on the shuttle, recommended to use with a Canbus toolhead board for less wires, but anything goes.
* Uses the Tap sensor to verify successful dropoffs and pickups.

See [Youtube](https://www.youtube.com/playlist?list=PLqU7kX5nUJDRDw5z0NLwJ22OkV6fbjnSW) for some action.

Preview

## Design

Toolheads are docked in an extra extrusion at the front of the printer. The toolhead is rested on a dock and as the shuttle moves down toolhead slides off the Tap rail.

Cudos for inspiration to [WP-Daksh](https://github.com/ankurv2k6/wp-daksh-toolchanger) and the Voron India discord.

The Tap probe is almost working as a toolchanger out of the box, the main issue is that a naked linear carriage is prone to loosing balls.
This is solved by pushing in a supporting TPU plug while the shuttle is traveling between the tools.

In a normal Tap setup, the plug would need to come from above the rail and no room for it there. So the MGN9 rail is flipped around - the carriage is on the shuttle side and the rail is on the toolhead side, allowing the plug to sit below the Tap rail in the dock.

# Work site here

This is **early build**, reliability is still unclear, significant changes likely. 

Done:
* The main shuttle + Stealthburner mount
* The dock works
* Put on a printer
* Make the distribution board
* Make the first print
* Iron out klipper setup.

WIP: 
* More instructions
* Mini stelthburner version, see [Tapchanger lite](https://github.com/viesturz/TapChanger-lite)
* Test, fix, repeat

## Known issues

* Tool Pickup Needs quite precise Y alignment to work reliably.

## Changelog

V0.2.5: Shuttle Design tweaks
 * MGN12 mounting position on shuttle to work with Mini SB.
 * Extra alignment guide to help line up with the rail.

V0.2: Tools are changin.
 * First successful print with ~50 changes.
 * Completely new dock, the rest slightly reworked.
 * Initial klipper setup. Tool auto-detection. Tap Z probe works across tools.

V0.1: It fits together.
 * Basic hardware assembly and operation works.
 * Real printing - still to be tested.

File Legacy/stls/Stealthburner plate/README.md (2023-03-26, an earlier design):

This is just the custom parts.

Please print The Upper part from [Tap repo](https://github.com/VoronDesign/Voron-Tap/tree/main/STLs).

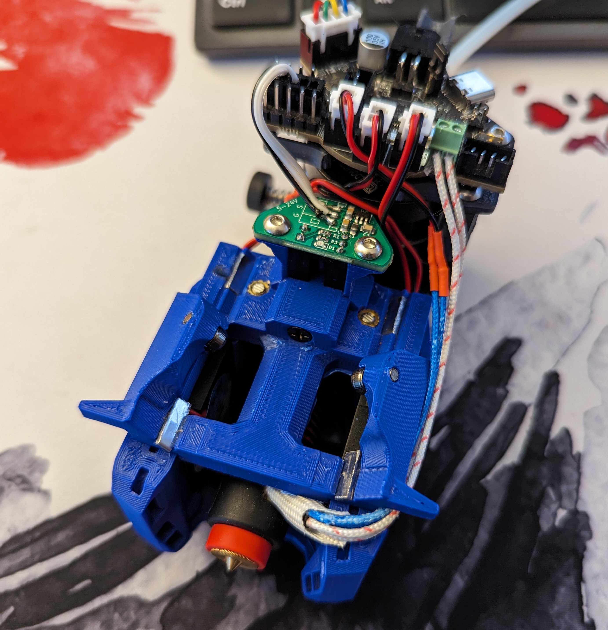
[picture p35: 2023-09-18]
images/plate.jpg

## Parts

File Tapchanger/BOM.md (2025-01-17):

# Bill of Materials (BOM)

## Rod Version

### Shuttle:
- **X6**: [MR83zz](https://google.com/search?q=MR83zz) bearings (3x8x3)
- **X6**: M3x8 button-head screws
- **X6**: M3 washers (0.5mm thickness)
- **X6**: Standard Voron heat-set inserts
- **X2**: 6x3mm round magnets

### Toolhead Mount Plate:
- **[OptoTap](https://google.com/search?q=optotap) sensor** (Required for Toolhead 0, optional for others)
- **X2**: M3x4 button-head screws (to mount the sensor)
- **X2**: 6x3mm round magnets
- **X2**: M3x8 SHCS screws (for tension adjustment)
- **Glue (optional)**: PVA glue works well to hold the rods/pads in place

### Version-Dependent:
- **Square Rods Version**:  
  - X2: 3x3mm square steel rods, 26mm long  
  - [AliExpress](https://aliexpress.com/w/wholesale-square-steel-rod-3mm.html) offers these (a bit stiffer than round rods).
- **Rods Version**:  
  - X2: 3mm steel rods, 26mm long

---

## Pads Version

### Shuttle:
- **X6**: [623](https://google.com/search?q=623+bearing) bearings (3x10x4)  
  - Can also use the flanged version from the regular Voron BOM.
- **X6**: M3x10 button-head screws
- **Remaining components**: Same as the rod version.

### Toolhead Mount Plate:
- **Pads Version**:  
  - X4: Steel pads (10x4mmx1.5mm)  
    - Cut from a stock piece available at local hardware stores.
- **Remaining components**: Same as the rod version.

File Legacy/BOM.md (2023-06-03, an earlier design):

## BOM

### Frame

The front needs to be extended 20 mm forward, and optinally top can be extended 40-60 mm up to give more vertical space.
For a 350 build, I'm using:
Front:
 * 20x20 extrusions: 2x533 + 3x470.
 * Two right angles to mount the center extrusion.
Top:
 * 20x40 extrusion 2x510mm + 2x470mm

### Shuttle
 * 8x M3 8mm BHSC for the [shuttle assembly](assembly.md). There is a 6mm option for those upgrading from a Voron Tap BOM.
 * 2x M3x6 countersunk steel screws (must be magnetic).
 * 1x 6x3mm round magnet for the carriage plug.
 
### Each Toolhead
 * A Tap kit + a Canbus enabled Stealthburner toolhead of your choice
 * 2x 5x2 round magnet, can use a 6x3mm magnet, but need to mod the bottom stealthburner screw holes to match.
 * **5amps** USB chargning cable, look for the ones supporting 100w, 1m, used for CANbus. Feel free to use other cables, I just like them being slim and thin.

### Each Dock
 * 2x M3x12 screws with thread dremeled off for the last 3 mm
 * 1x 6x3 round magnet
 * 3x m3x12, 1x m3x10
 * Some silicone for the nozzle pad
 * a small piece of spring to hold up the nozzle pad.
 
### Distribution board
 * Prototyping board ~100mm x 4 holes
 * 6x KF128 2.54mm pitch 4pin PCB screw Terminal block, rated for 6-10amps.
 * 2x m3x12, 2x heatset inserts

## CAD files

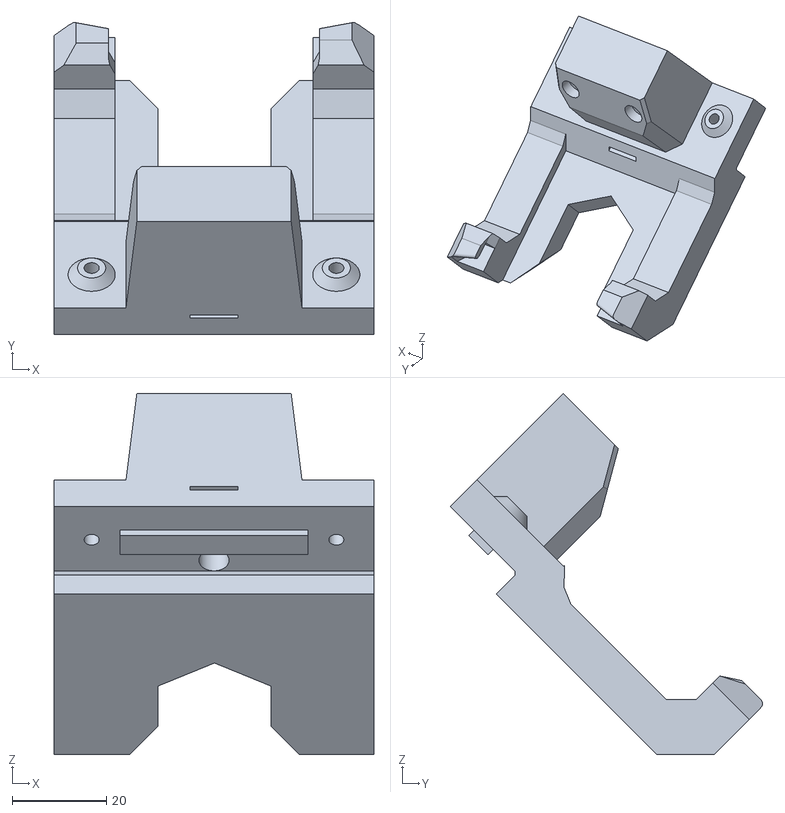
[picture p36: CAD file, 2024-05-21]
Dock/Crossbar/Xol-Toolhead_Dock.stl
68.0 x 66.3 x 76.7

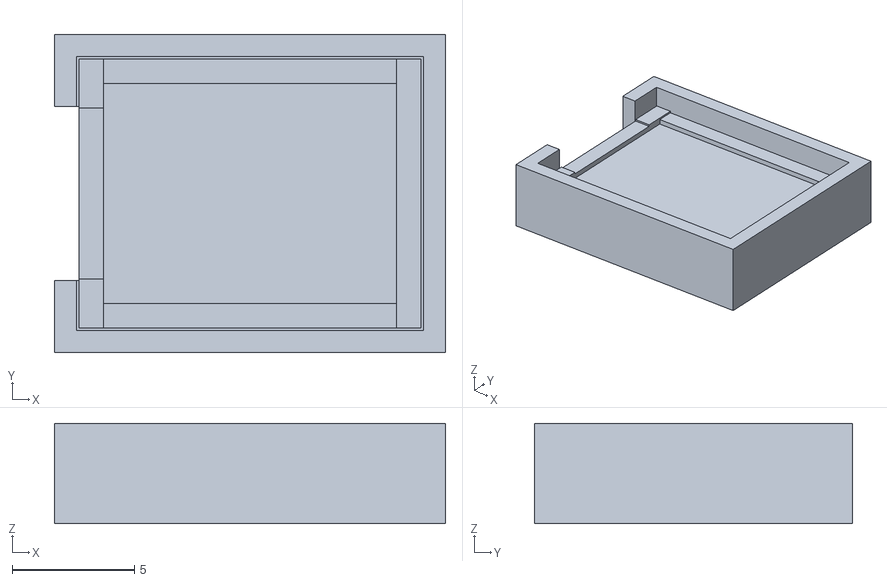
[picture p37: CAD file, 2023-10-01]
Dock/Jigs/Nozzle Pad Mold A.stl
16.0 x 13.0 x 4.10

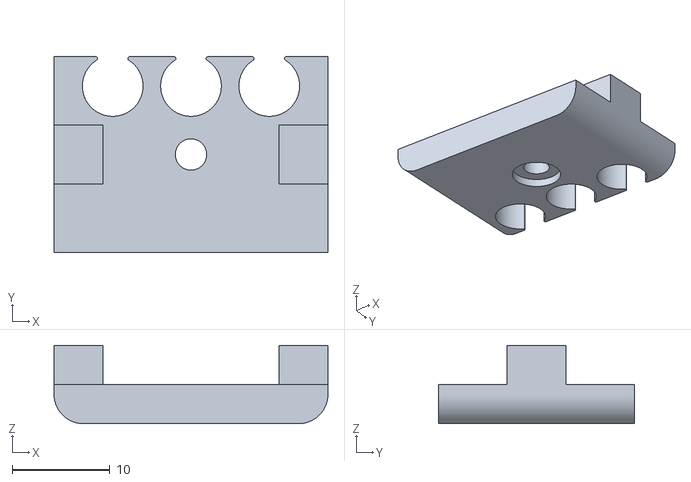
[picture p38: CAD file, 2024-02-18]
Dock/Liftbar/AntidropMagnet/Top.stl
28.0 x 20.0 x 8.00

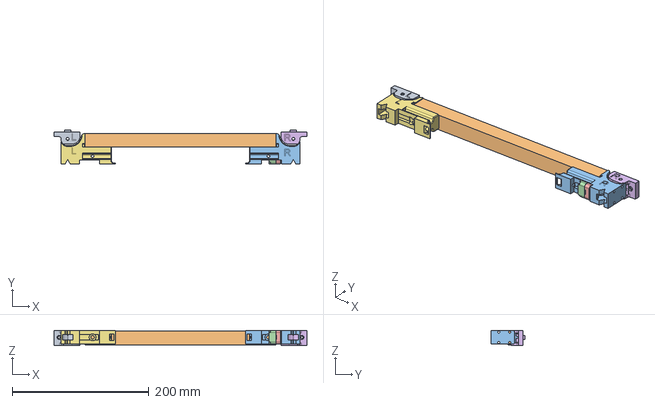
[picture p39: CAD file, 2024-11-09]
Dock/Liftbar/CAD/Liftbar on Rails Two Loops.step
370.0 x 50.0 x 22.0 mm

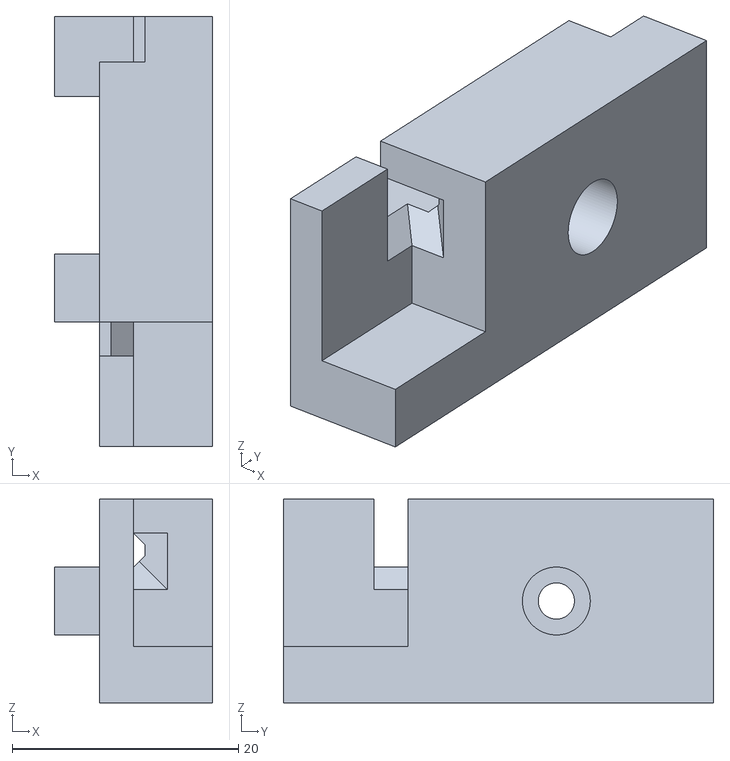
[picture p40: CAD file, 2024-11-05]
Dock/Liftbar/Endstop Bottom Left D2F.stl
14.0 x 38.0 x 18.0

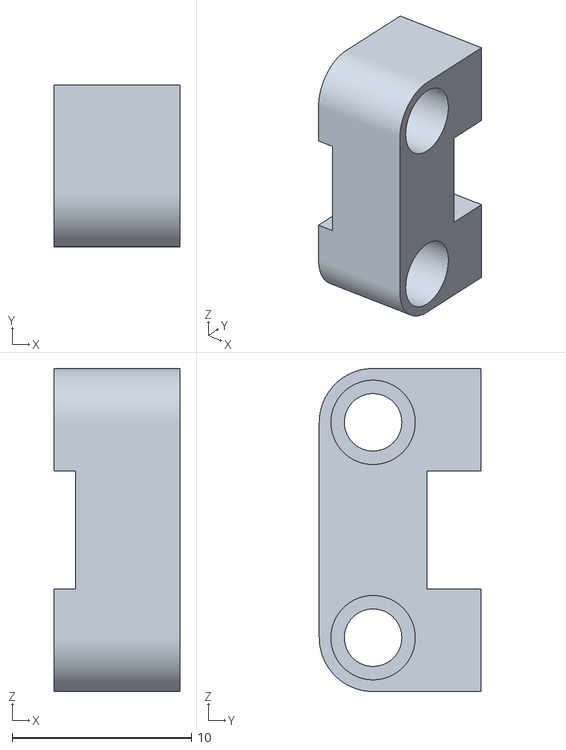
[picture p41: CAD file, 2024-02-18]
Dock/Liftbar/Gantry Continuous Loop/Belt Tensioner B.stl
7.00 x 9.00 x 18.0

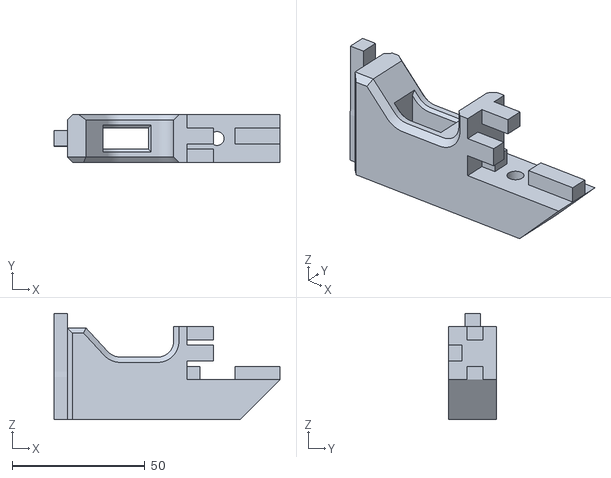
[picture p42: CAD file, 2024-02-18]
Dock/Liftbar/Gantry Continuous Loop/GrooveSlider/Brace-Left.stl
85.0 x 18.0 x 39.9

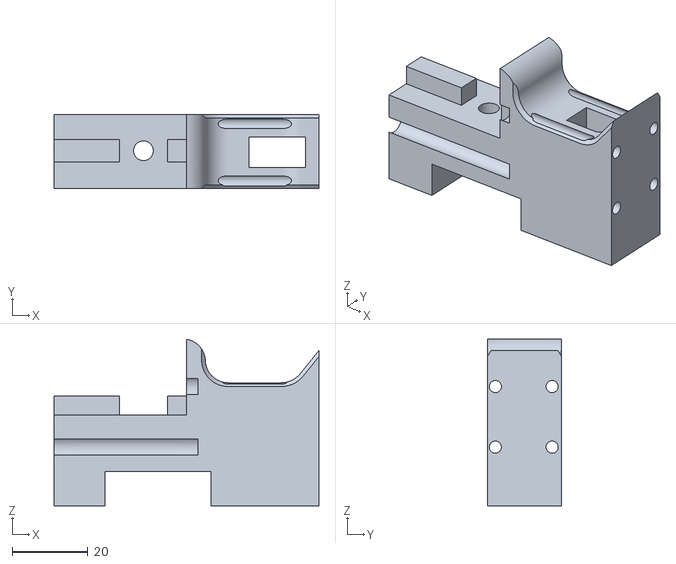
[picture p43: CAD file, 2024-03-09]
Dock/Liftbar/Gantry Continuous Loop/MGN9H/Brace Right.stl
70.0 x 19.6 x 44.0

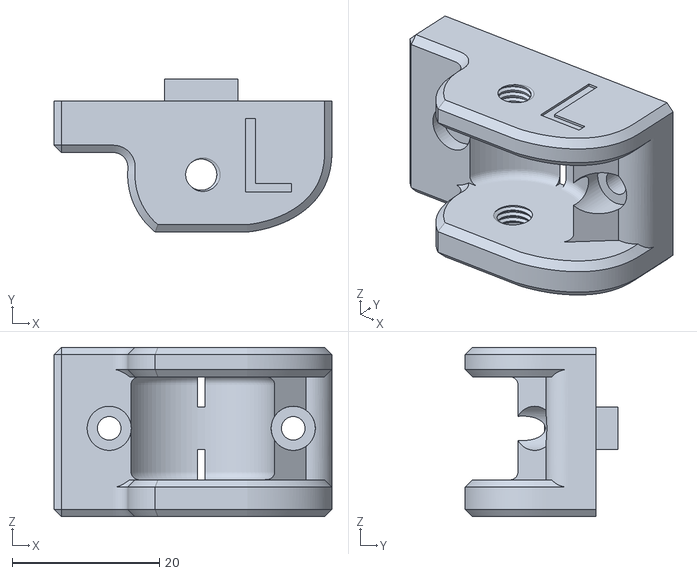
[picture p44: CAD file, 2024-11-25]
Dock/Liftbar/Gantry Independant Loops/Idler Left m5.obj
37.8 x 20.8 x 23.0

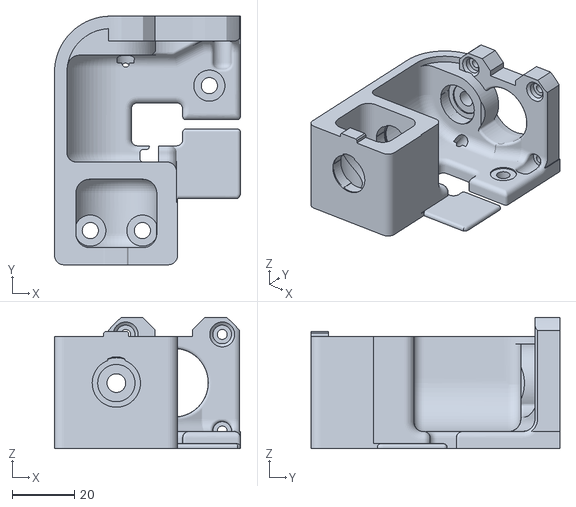
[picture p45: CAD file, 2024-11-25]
Dock/Liftbar/Gearbox - 2.4/Housing Right.obj
59.7 x 79.8 x 42.2

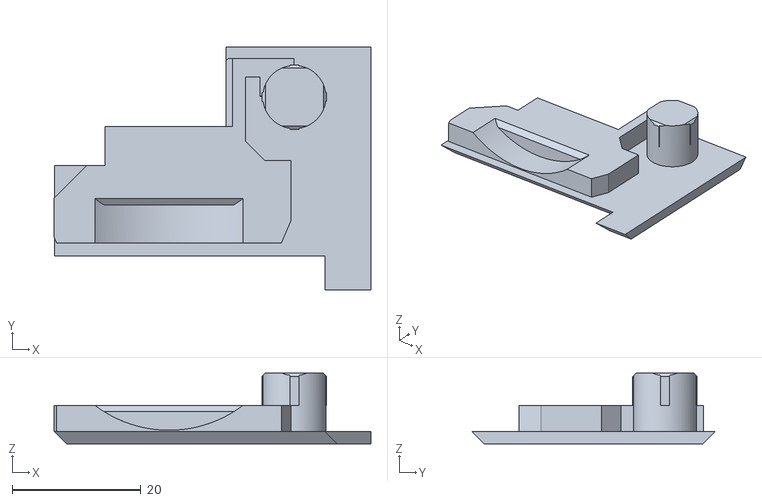
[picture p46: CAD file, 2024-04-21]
Dock/Liftbar/Gearbox - Trident/Lid-left.stl
49.2 x 37.8 x 11.0

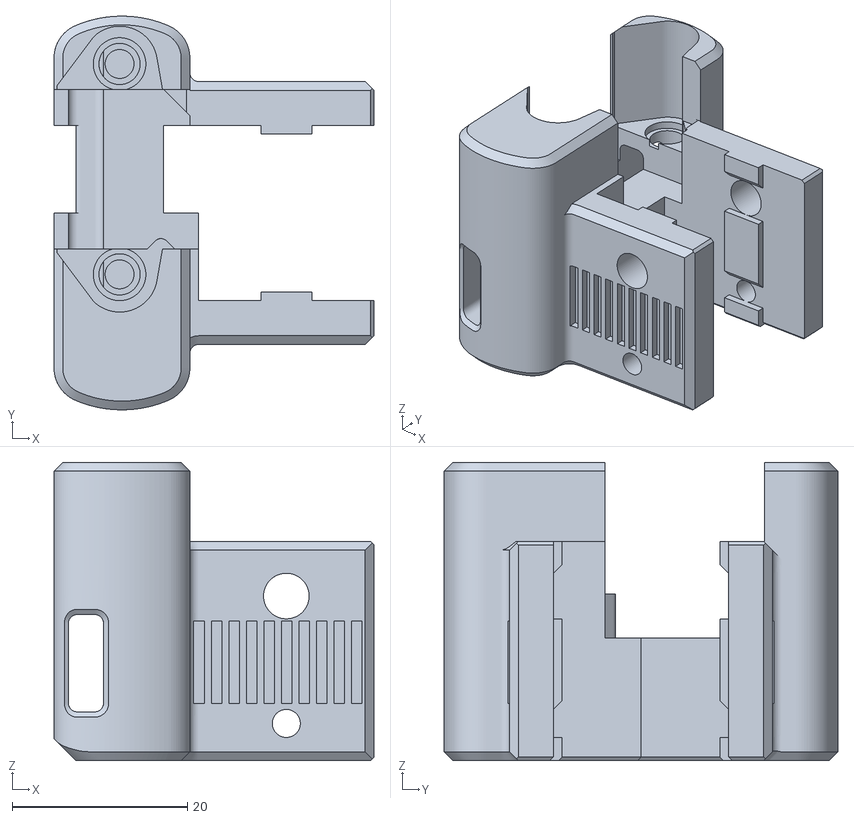
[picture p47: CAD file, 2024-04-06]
Dock/Liftbar/XY Idlers - 2.4/Housing.stl
36.5 x 44.9 x 34.0

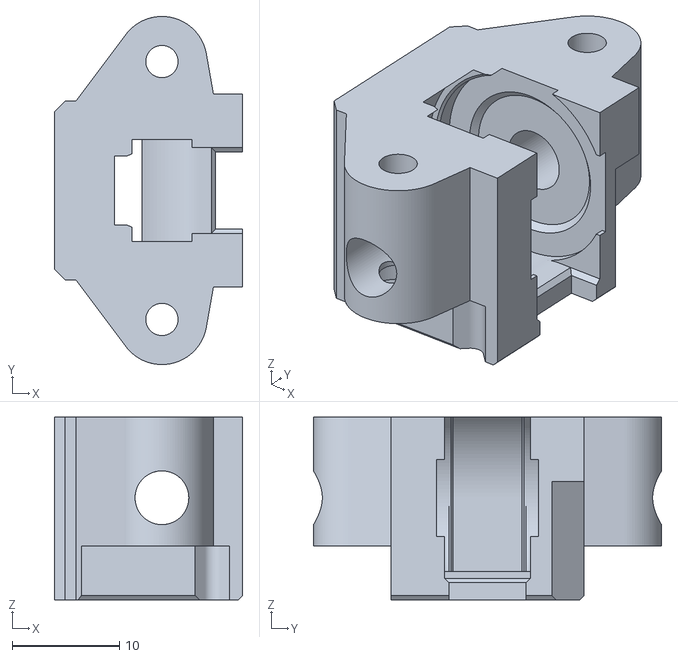
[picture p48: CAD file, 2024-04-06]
Dock/Liftbar/XY Idlers - Trident/Slide.stl
17.5 x 32.4 x 17.0

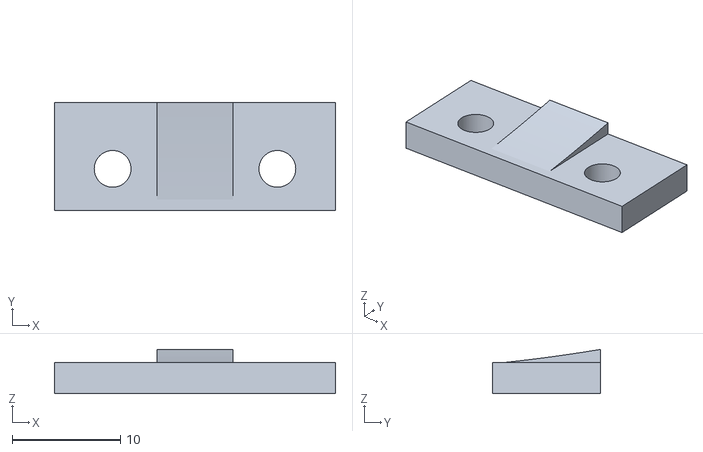
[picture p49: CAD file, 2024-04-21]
Dock/NozzelPadClip-Dragon.stl
26.0 x 10.0 x 4.09

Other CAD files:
Dock/Top/RapidBurner.stl
Dock/Trident/Servo clip Left.obj
Extras/Dragon burner + HGX 2 Gears/Front-Bambu.obj
Extras/Dragon burner + HGX Gears/Back.stl
Dock/Crossbar/Deprecated/DragonBurner Dock Magnets.stl
Dock/Crossbar/DockMount.stl
Dock/Crossbar/DragonBurner Dock Magnets.stl
Dock/Crossbar/DragonBurner.stl
Dock/Crossbar/MiniStealthburner Dock.stl
Dock/Crossbar/RapidBurner.stl
Dock/Crossbar/Stealthburner Dock.stl
Dock/Crossbar/Stealthburner DockMount.stl
Dock/Jigs/Nozzle Pad Mold B.stl
Dock/Liftbar/AntidropMagnet/Bottom.stl
Dock/Liftbar/CAD/XY Idlers.step
Dock/Liftbar/DragonBurner - Dock.stl
Dock/Liftbar/DragonBurner - DockMount.stl
Dock/Liftbar/Endstop Bottom Left D2S.stl
Dock/Liftbar/Endstop Bottom Rght D2F.stl
Dock/Liftbar/Endstop Bottom Right D2S.stl
Dock/Liftbar/Gantry Continuous Loop/Belt Tensioner A.stl
Dock/Liftbar/Gantry Continuous Loop/GrooveSlider/Belt Clamp-Left.stl
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

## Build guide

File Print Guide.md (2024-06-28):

# Print guide

The plastic parts are bearing quite some load, so printing them accurately key to a succeessful setup.

### Plastic

Polycarbonate is the recommended option, being extremely rigid. And requires no glue to hold the inserts in.

ASA is the next best option, providing generally better rigidity than ABS, especially when kept under load. I have had good success with Prusament ASA.

CF-ASA is also fine. I did not see significnant delta from plain ASA however.

### Parameters

Use usual [Voron print settings](https://docs.vorondesign.com/sourcing.html#print-settings), plus:

 - 80% infill.
 - Supports on bed plate only.
 - external layers first, or second if your slicer has it.
 - (optional) Enable ironing.
 - support interface layers: 2
 - support interface spacing: 0.12
 - I'm printing with organic suppots on build plate only, but anything goes

### Cleanup

You will need to clean up some supports.  Flush cut pliers will get them removed just fine.

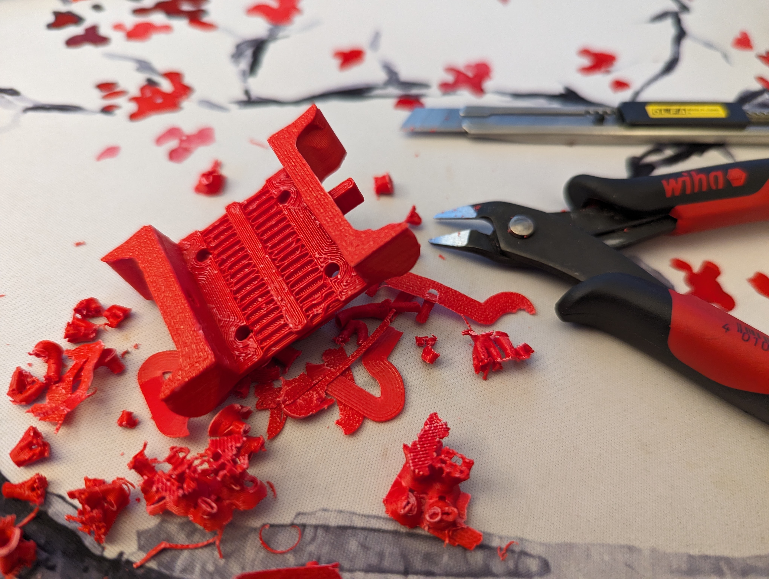
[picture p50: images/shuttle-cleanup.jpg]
Cleanup


Optionally can print with PETG or soluable supports, but I would not bother.

### Aluminium shuttle

SLS printining the shuttle from aluminium is expensive but adds significant stiffness bonus over ASA. Similar to polycarbonate.

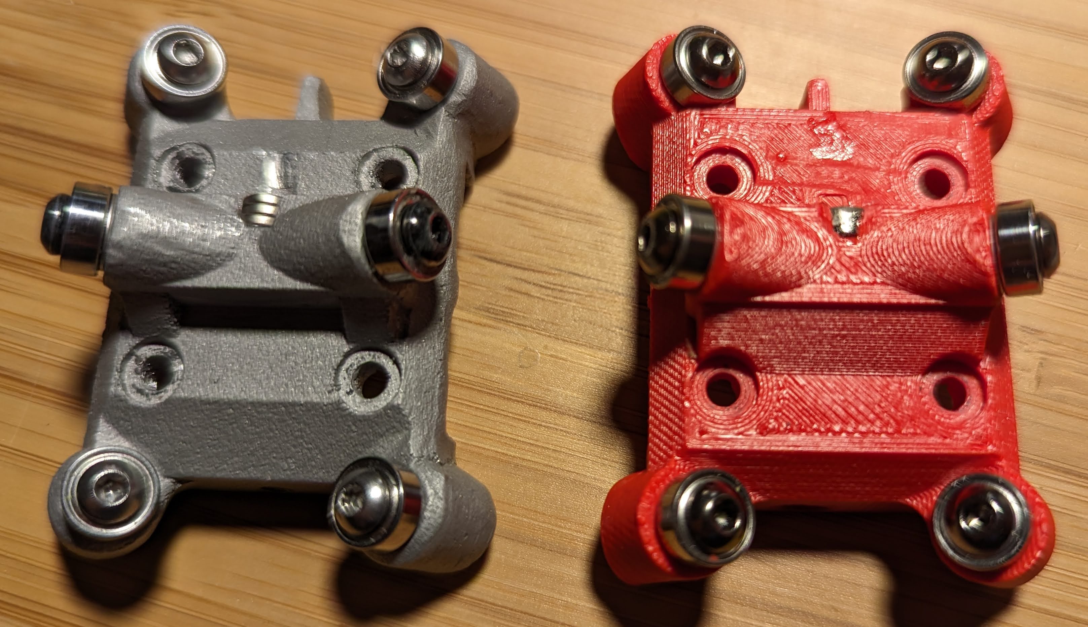
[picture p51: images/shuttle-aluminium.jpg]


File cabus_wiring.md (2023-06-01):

# Canbus Wiring

There is no requirement to use Canbus with TapChanger, but it's the most supported method right now.
Alternatively each toolhead can be connected via USB or have a big fat wire cable to a controller board that supports multiple extruders.

## Canbus topology.

Canbus is essentially a mini Ethernet, over a shared wire pair. 
Each node is connected in parralel.

This is the overall layout we are using for wiring:

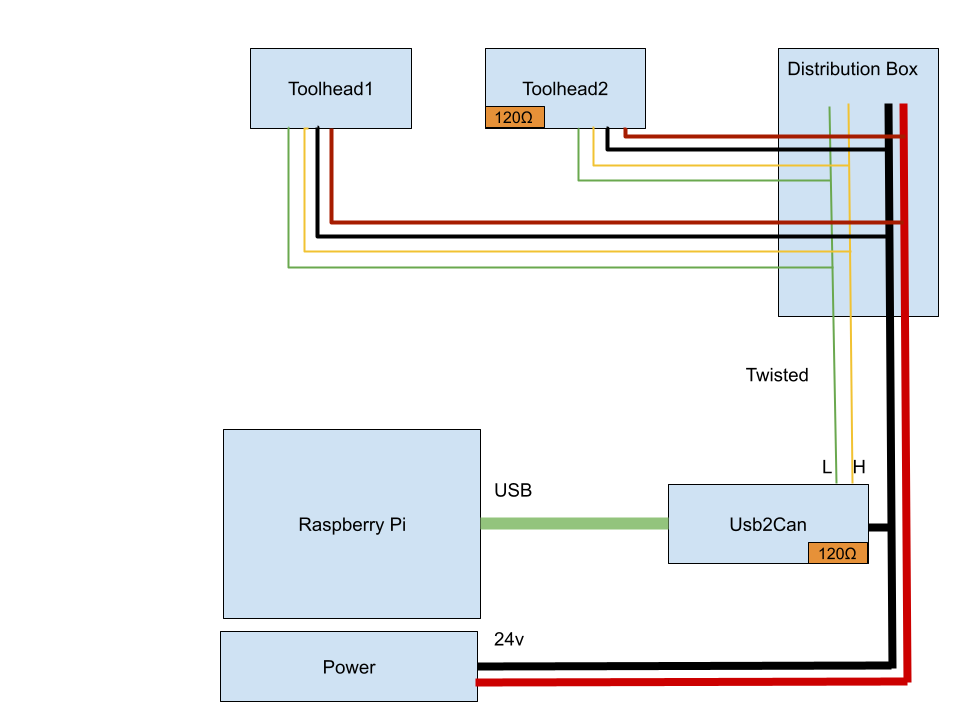
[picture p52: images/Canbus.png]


Each extruder gets:

* Ground and +24V
* CanL and CanH

CanL and CanH wires need to be twisted togeteher. Premade Canbus wire harnesses are available, but distances we are using here are very small and just manual twisting is fine. 

Calculate your max load across all hotends, and make sure that the wires from the distrbution box down to PSU can handle that.
The heaters are typically controlled with 100ms power cycle that means that even if they are all on 10%, they **will** be on at 100% at the same time for 100ms at a time which is enough to brownout your PSU. I had very wierd Canbus glitches that came down to voltage drops when all heaters are on.

Maybe one day Klipper will support power cycle staggering making this less of a problem. 

## Canbus speed

Canbus supports a range of speeds up to 1mbs.
We are using an unusual topology with fairly long branches from from the main bus, which causes extra signal reflections. There are quite a few data sheets describing the maximum branch length for each speed, I have seen very conservative saying 30cm max for any speed to very relaxed of 1.5M for 1mbs.

Our branch length from the distribution box is approx 60cm. That definately seems iffy for 1mbs and seems confortable for 500kbs.
That is what I'm running. And getting about 5% utilization running two tooleahds so seems plenty of headroom.

## Canbus Toolhead boards

There are several extruder boards that are specifically designed for Stealthburner. 
Most notably [EBB SB2209](https://biqu.equipment/products/bigtreetech-ebb-sb2209-can-v1-0) from Bigtreetech and [SB2040](https://www.google.com/search?q=SB2040) from Mellow fly. I have had good success with both.

Similary for Mini stealthburner there are smaller versions available, like [EBB36](https://biqu.equipment/products/bigtreetech-ebb-36-42-can-bus-for-connecting-klipper-expansion-device).

All of those boards can be used either in Canbus or USB mode, changeable by flashing the appropriate firmware. If you are uncomfortable with Canbus, and fine with running two more wires to each hotend, you can use USB mode with a USB hub.

The flashing and setup process of those boards can be a bit involved, the manufacturers instructions are okay, but genereally require a Windows machine to follow. There are [some instructions](https://mpx.wiki/flash-m8p-and-ebb-sb-toolboard) out there to flash directly from Raspberry. 

## Raspberry pi to canbus

Raspberry pi does not support Canbus directly, there are a few options what to use.

### Usb2Can adapter

This seems to be the most reliable option. But costs extra and occupies a USB port on your Pi

### Builtin Can port in your controller board.

To enable this, you need to flash Klipper with U2C enabled. If your board supports this, there should be a guide for that.

In my experience this can be a bit unreliable. Your main controller board is also now connected via CanBus and now needs to drive 6 more motors and bunch of fans and thermistors. This leads to about 50% of bandwidth saturnation with 500kbs. 

I did see occasional probe move timeouts with it so moved to a dedicated Usb2Can board instead.

### Canbus hats

Are a Raspberry PI hat boards that use the GPIO pins instead of USB. Should work just fine, have not tired though.

## Power supply

My rule of thumb: Sum up all your hotend heaters + ~10w on top for each hotend + ~100w for the rest of the printer (assuming mains heated bed).

## Wiring it up.

I'm running oversized 12gauge cables from distribution box to PSU. Mainly because the next ones I had around where significanly thinner.

And running USB C charging cables from hotend to the distribution box. Get ones that are arvertised for 100W charging. They are supposed to handle 5A sustained. That is 120w - more than enough for most hotends. Rapido or other 100w+ hotends are a bit marginal.
The USB cables are significantly more lightweight and felxible than premade Canbus harnesses and with Silicone sleeving should survive long enough. USB data cables are also twisted pair, making it a nice match.

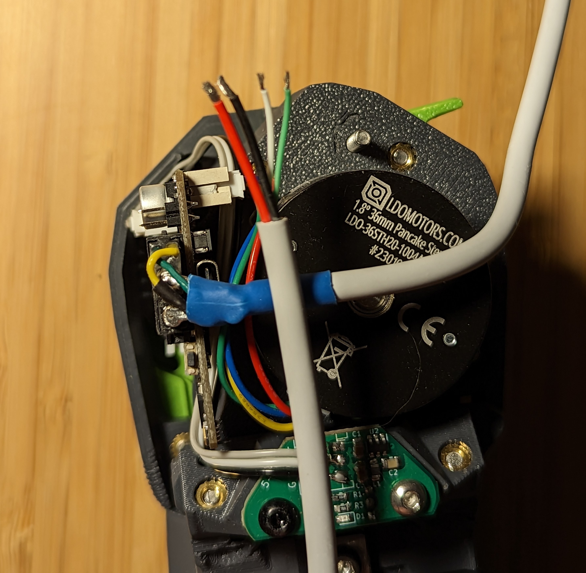
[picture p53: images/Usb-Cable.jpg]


For Distribution box to Usb2Can, I just manually twisted together two wires.

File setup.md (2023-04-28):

# Setup & troubleshooting

## Mounting

Mount toolhead X rail. Mine is sitting 20cm below the top, which is pretty close to the ceiling. 

Mount the docks on the rail. Do not tighten, will adjust them later.
Adjust the back screws so that the pivot is not loose anymore.

Install the toolheads in the docks, except #0, that is mounted on the shuttle.

## Software config

See the Klipper folder for my config. This is still evolving so you will need to know how to manually install. If you don't the rest is probably too advanced anyway.

Before proceeding further, you should have all the toolheads configured, endstop offsets setup, toolhead offsets setup. Essentially able to print with each toolhead independantly.

Tool 0 will have offset 0 and the rest of the tools will have some offsets.

See [NozzleAlign](https://github.com/viesturz/NozzleAlign) on my offsets tool. Or anything else out there.

## Dock align

Each dock needs alignment coordinates in the tools.cfg. 
To get them, home with your tool0 - and remove it from the shuttle and place it back into the dock, leaving shuttle with the plug installed.

Now for each tool, position the shuttle so that the empty carriage is exactly below the tool rail.
With X and Y aligned and Z so that there is no gap and also no overlap with tool rail. 

The rail should be ever so sligthly over it's normal position, it tends to move back during mounting. A good guess is it covering the entire carriage opening. You will be able to adjust it later with the screws.

Preview

Write down the coordinates, this is your **park* position for the tool.

Test dock alignment by moving Z up ~20mm. The toolhead should slide into the shuttle without too much judder. At this point you want to tighthen the dock screws.

## Testing

** Be prepared to drop some balls** The first try will likely fail, make sure you can collect any balls flying off the printer. Closing printer doors is a good idea. Removing the flex plate is a good idea - makes the bed less bouncy.

Start with tool 0 mounted and issue the commands to mount next tool. The unmounting usually is fine, any alignment problems will pop up in the mounting process when the shuttle starts moving up. 

**Keep your hand on the toolhead** to help it along if it gets stuck. The most frequent problem is that the toolhead is too far back. Adjust the back screws to compensate.

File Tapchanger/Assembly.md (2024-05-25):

# The Shuttle

Print the shuttle and endstop attachment of choice. Clean up all the supports. 

|  |  |
| -- | -- |
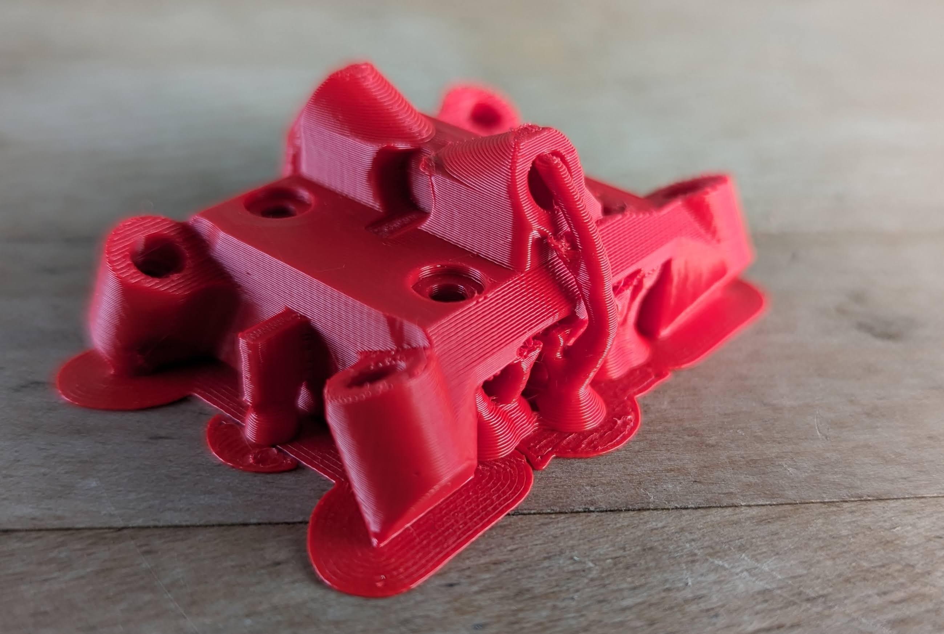
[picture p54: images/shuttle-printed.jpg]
Printed
|  | Cleaned up |

Insert the heat-set inserts, they need to be flush with the surface and at a reasonably accurate angle.
Use the positioning jig for vertical insert direction.

|  |  |
| -- | -- |
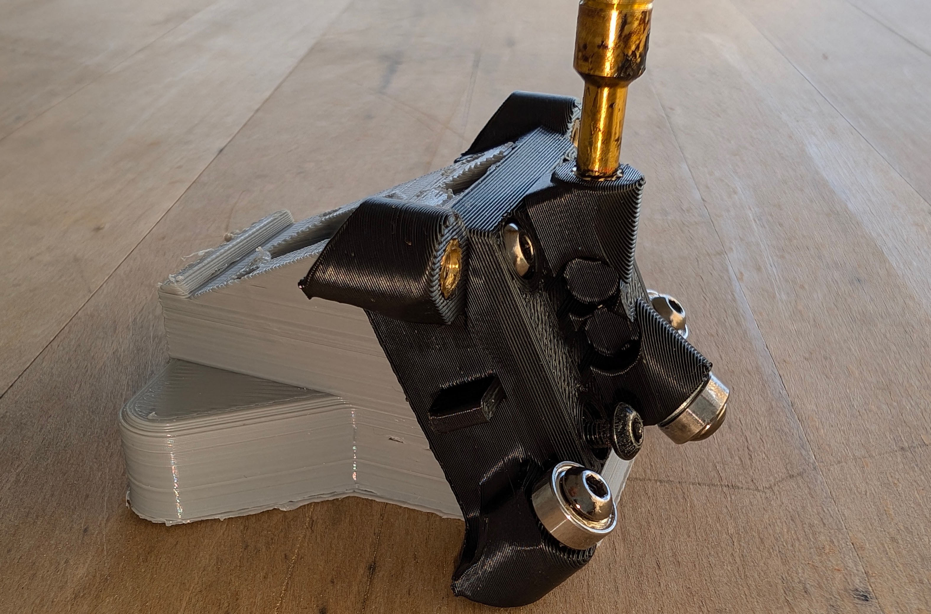
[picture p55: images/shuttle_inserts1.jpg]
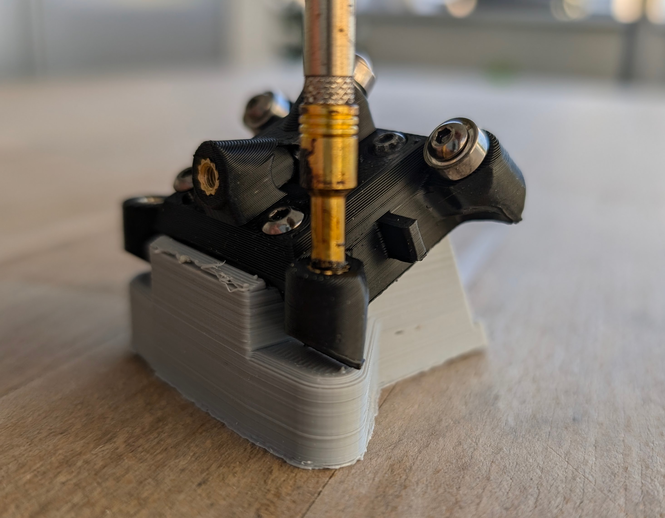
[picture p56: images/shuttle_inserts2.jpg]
|  |  |

Screw in the bearings, using 8-10 mm screws and washers. They should lock in quite tight, optionally can add locktite for extra safety.

Glue in the magnet. It should be flush or slightly recessd.

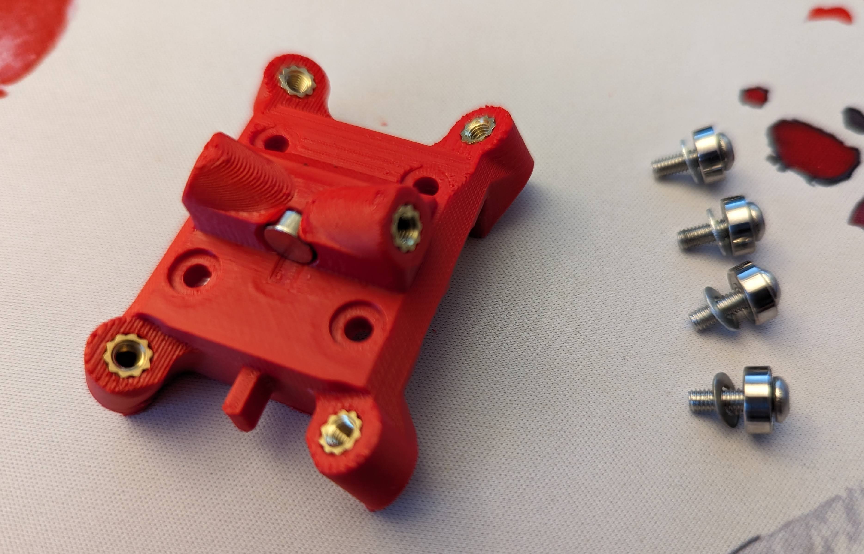
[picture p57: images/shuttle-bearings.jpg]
Preview


# The toolhead plate

(Round rods) Use a 3mm drill bit on slow speed to clear out any loose overhangs from the rod holes.

Cut rods to length and push in as far as they go.
I'm adding some PVA glue to the holes to hold them but still be able to remove if needed.

Thread in 2 m8 socket head screws at the bottom. All the way in should be too loose, back up both a bit at the time to get a snug fit.

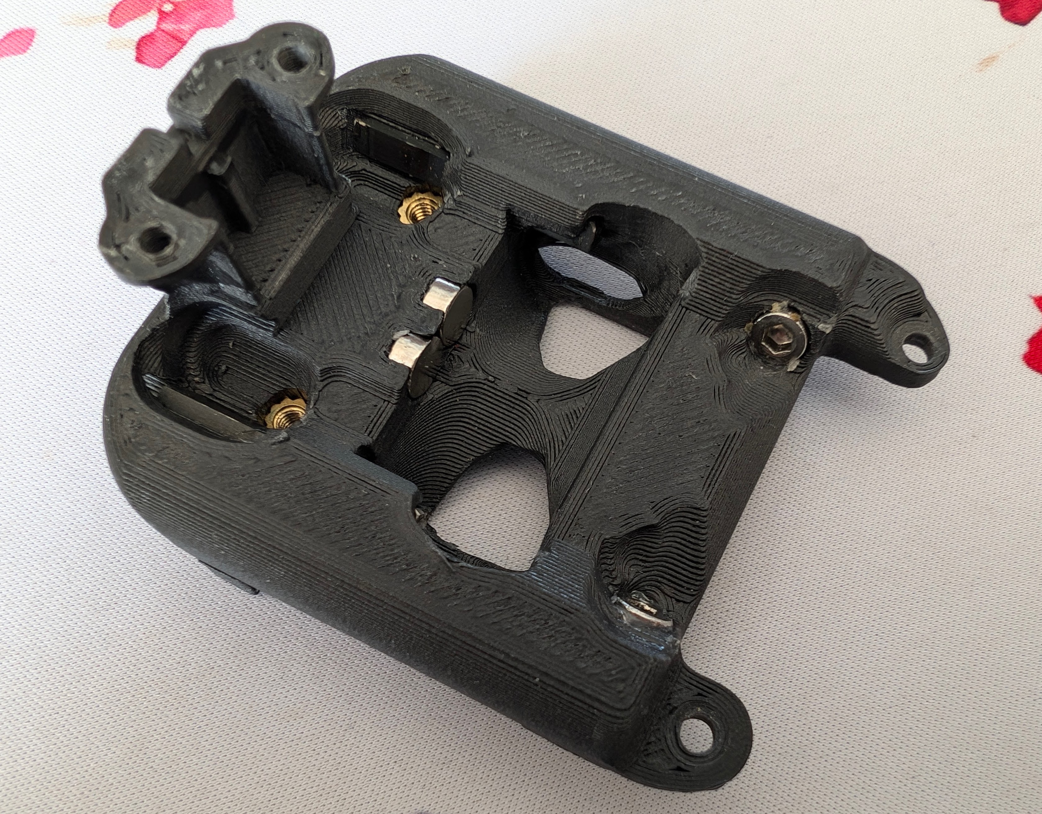
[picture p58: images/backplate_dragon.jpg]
Toolhead plate finished


## Tuning the tension

General rule of thumb - the tightest that runs well. There shuld be some back pressure when clicking together. But not much more than the weight of the hotend.

When clicking together, both bolts should contact the bearings simultaneously. Them being off too much will cause some unwanted twisting loads. I have not paid much attention to getting this exactly right and have not had any problems.

Final step - add a drop of CA glue at the base for the scew head to lock it in place.

## Tension and temperature

Chamber temperature has effect on the tension. Generally less tension at higher temps.

* ASA: The tension will lessen with higher chamber temps, but return to previous level on cooldown.

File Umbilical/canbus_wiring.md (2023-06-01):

# Canbus Wiring

There is no requirement to use Canbus with TapChanger, but it's the most supported method right now.
Alternatively each toolhead can be connected via USB or have a big fat wire cable to a controller board that supports multiple extruders.

## Canbus topology.

Canbus is essentially a mini Ethernet, over a shared wire pair. 
Each node is connected in parralel.

This is the overall layout we are using for wiring:

Preview

Each extruder gets:

* Ground and +24V
* CanL and CanH

CanL and CanH wires need to be twisted togeteher. Premade Canbus wire harnesses are available, but distances we are using here are very small and just manual twisting is fine. 

Calculate your max load across all hotends, and make sure that the wires from the distrbution box down to PSU can handle that.
The heaters are typically controlled with 100ms power cycle that means that even if they are all on 10%, they **will** be on at 100% at the same time for 100ms at a time which is enough to brownout your PSU. I had very wierd Canbus glitches that came down to voltage drops when all heaters are on.

Maybe one day Klipper will support power cycle staggering making this less of a problem. 

## Canbus speed

Canbus supports a range of speeds up to 1mbs.
We are using an unusual topology with fairly long branches from from the main bus, which causes extra signal reflections. There are quite a few data sheets describing the maximum branch length for each speed, I have seen very conservative saying 30cm max for any speed to very relaxed of 1.5M for 1mbs.

Our branch length from the distribution box is approx 60cm. That definately seems iffy for 1mbs and seems confortable for 500kbs.
That is what I'm running. And getting about 5% utilization running two tooleahds so seems plenty of headroom.

## Canbus Toolhead boards

There are several extruder boards that are specifically designed for Stealthburner. 
Most notably [EBB SB2209](https://biqu.equipment/products/bigtreetech-ebb-sb2209-can-v1-0) from Bigtreetech and [SB2040](https://www.google.com/search?q=SB2040) from Mellow fly. I have had good success with both.

Similary for Mini stealthburner there are smaller versions available, like [EBB36](https://biqu.equipment/products/bigtreetech-ebb-36-42-can-bus-for-connecting-klipper-expansion-device).

All of those boards can be used either in Canbus or USB mode, changeable by flashing the appropriate firmware. If you are uncomfortable with Canbus, and fine with running two more wires to each hotend, you can use USB mode with a USB hub.

The flashing and setup process of those boards can be a bit involved, the manufacturers instructions are okay, but genereally require a Windows machine to follow. There are [some instructions](https://mpx.wiki/flash-m8p-and-ebb-sb-toolboard) out there to flash directly from Raspberry. 

## Raspberry pi to canbus

Raspberry pi does not support Canbus directly, there are a few options what to use.

### Usb2Can adapter

This seems to be the most reliable option. But costs extra and occupies a USB port on your Pi

### Builtin Can port in your controller board.

To enable this, you need to flash Klipper with U2C enabled. If your board supports this, there should be a guide for that.

In my experience this can be a bit unreliable. Your main controller board is also now connected via CanBus and now needs to drive 6 more motors and bunch of fans and thermistors. This leads to about 50% of bandwidth saturnation with 500kbs. 

I did see occasional probe move timeouts with it so moved to a dedicated Usb2Can board instead.

### Canbus hats

Are a Raspberry PI hat boards that use the GPIO pins instead of USB. Should work just fine, have not tired though.

## Power supply

My rule of thumb: Sum up all your hotend heaters + ~10w on top for each hotend + ~100w for the rest of the printer (assuming mains heated bed).

## Wiring it up.

I'm running oversized 12gauge cables from distribution box to PSU. Mainly because the next ones I had around where significanly thinner.

And running USB C charging cables from hotend to the distribution box. Get ones that are arvertised for 100W charging. They are supposed to handle 5A sustained. That is 120w - more than enough for most hotends. Rapido or other 100w+ hotends are a bit marginal.
The USB cables are significantly more lightweight and felxible than premade Canbus harnesses and with Silicone sleeving should survive long enough. USB data cables are also twisted pair, making it a nice match.

Preview

For Distribution box to Usb2Can, I just manually twisted together two wires.

## Connecting via the distribution board PCB

The `electronics` folder contains a PCB that can be used to connect the canbus cables together. It has 7 connectors: one to your controller board, and 6 for extruders. The PCB itself can be ordered online (e.g. from PCBWay, by uploading `Distribution_Board_cam_output.zip` which contains gerbers). It is meant to accomodate 4-pin JST-XH male connectors (e.g. [these from amazon](https://a.co/d/690GuEG)).

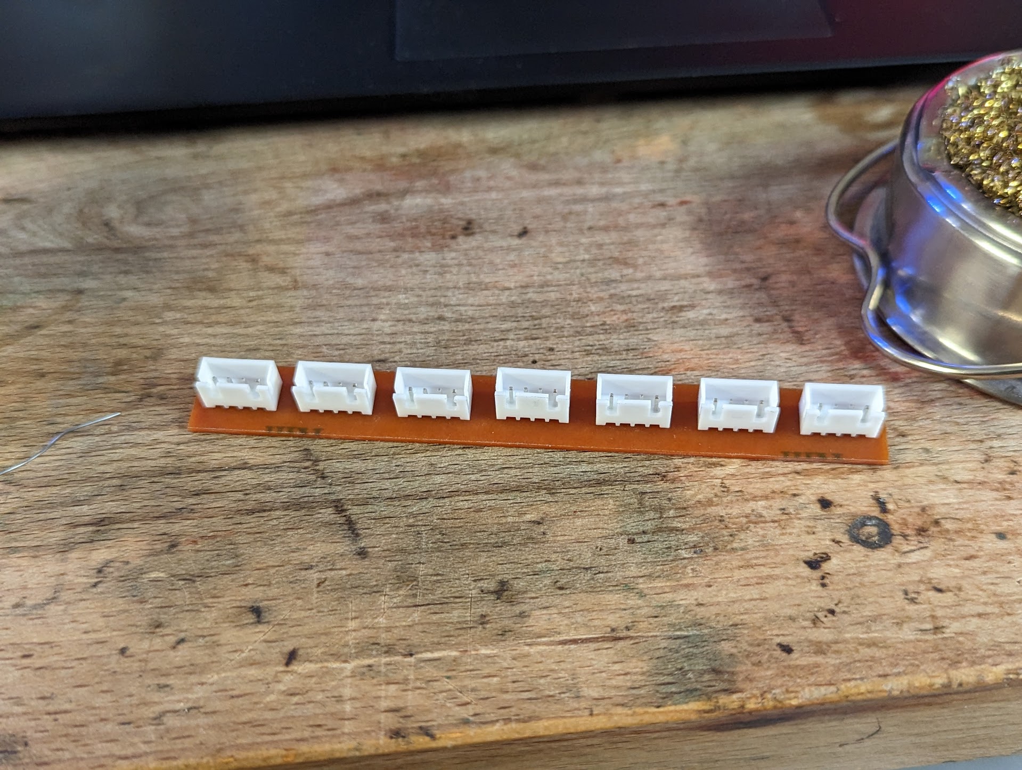
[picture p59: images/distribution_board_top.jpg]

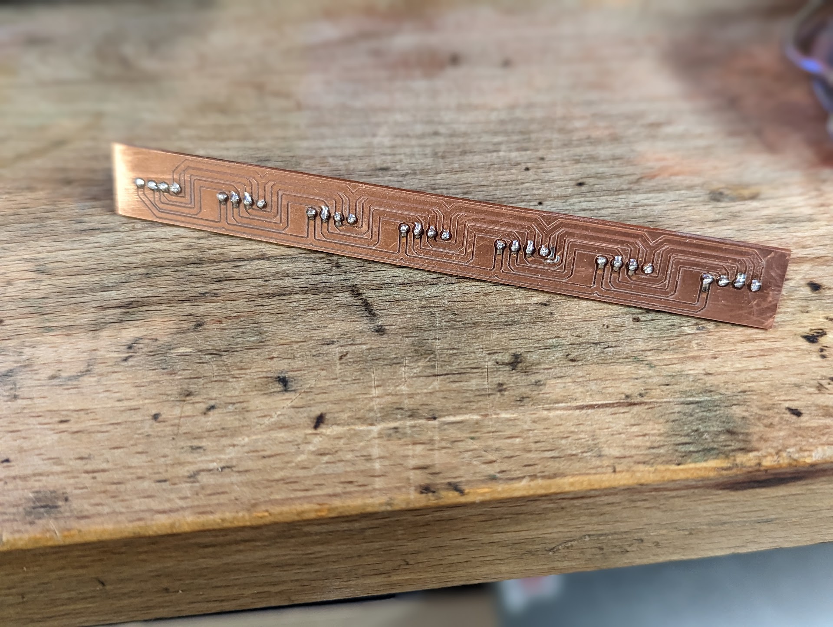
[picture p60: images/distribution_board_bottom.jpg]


For a voron 2.4 350mm build, cutting the cables to 1 meter in length should be long enough to go from the toolhead to the distribution board. If you are using BTT SB2209/SB2240 boards, they come with a wire long enough that you will have spare length to connect the distribution board to your controller as well. Simply crimp the female JST-XH connectors with a crimping tool like [this one](https://a.co/d/giwkw9a).

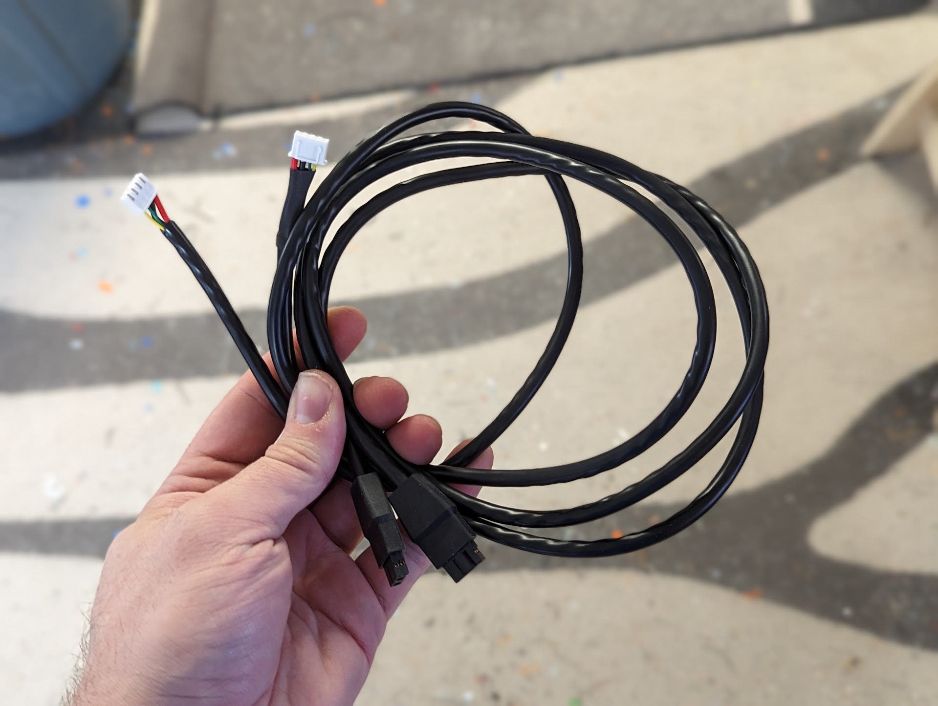
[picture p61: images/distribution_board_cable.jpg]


Use some double-sided tape and fit the board inside the distribution box:

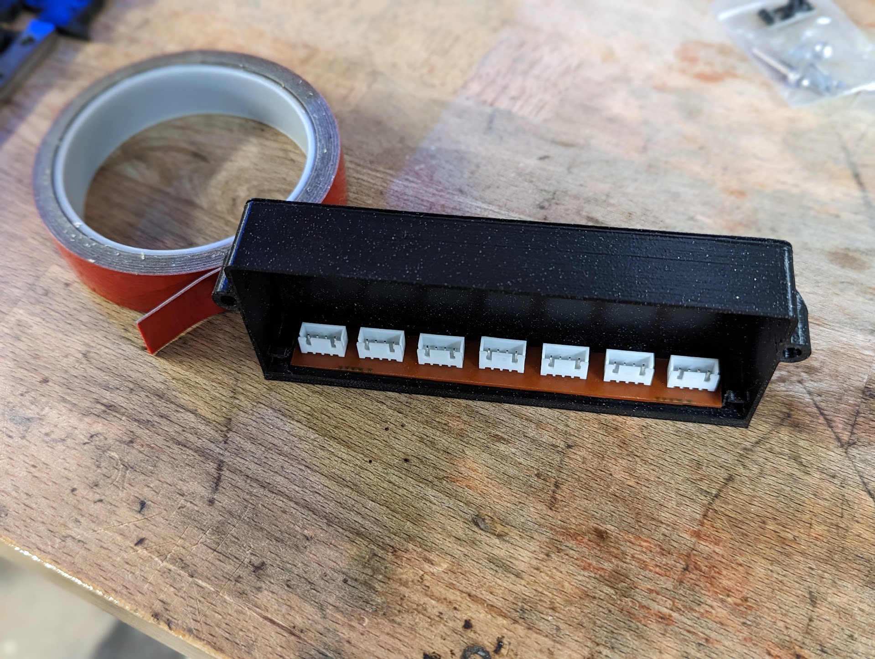
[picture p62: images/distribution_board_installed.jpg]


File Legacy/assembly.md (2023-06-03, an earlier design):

# The Shuttle

Print one copy of the plug and glue the magnet into place.
I used 82 hardness TPU, but mostly anything should work. Possibly even regular ABS.
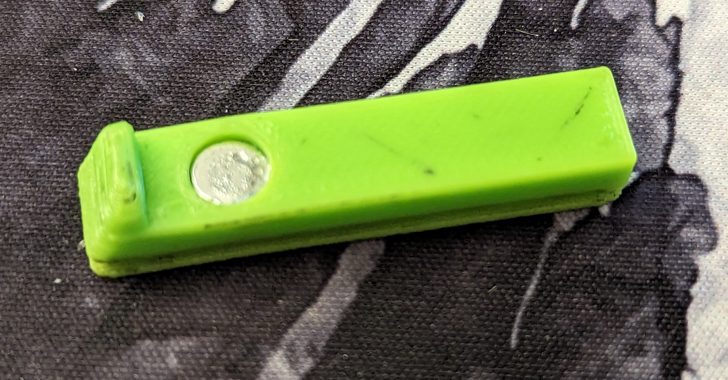
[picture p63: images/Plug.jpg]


The shuttle needs to be printed with supports. And the screws are partially covered by the rail carriages.

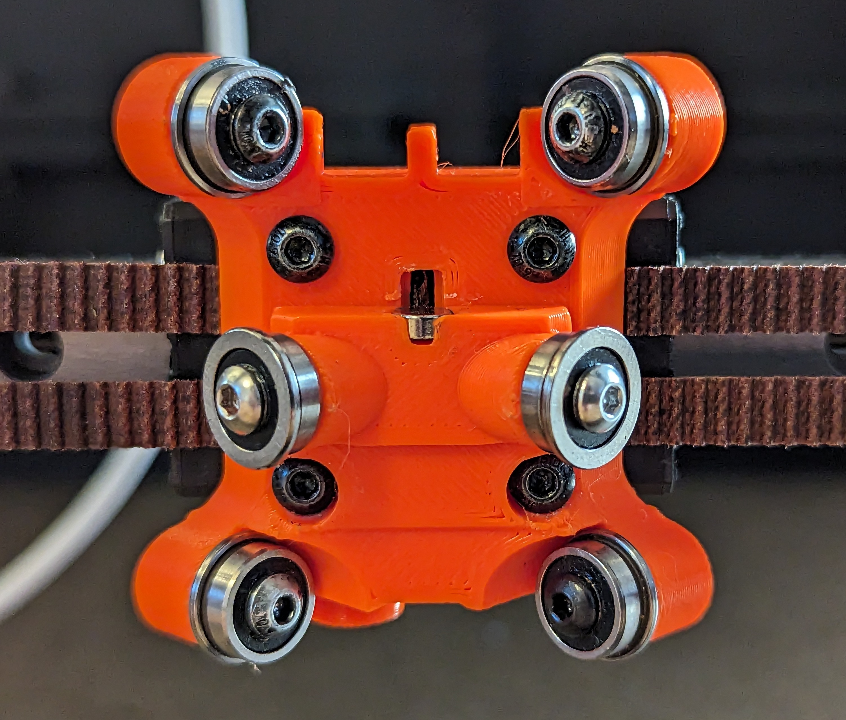
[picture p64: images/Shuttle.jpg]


First insert all the screws into the part. 

Then screw in the MGN9 carriage. 

Then attach your belts and locate the shuttle over the main carriage.

Use a ball end allen key inserted at a slight angle to screw in the MGN12 carriage.

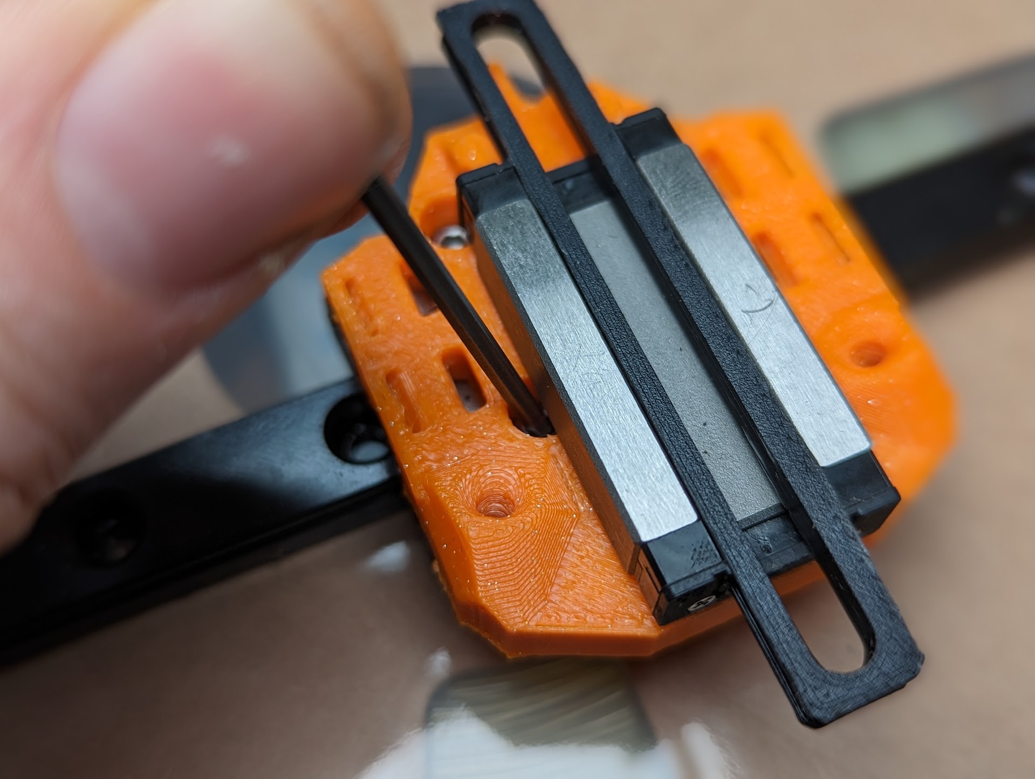
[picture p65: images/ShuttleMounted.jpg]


The X endstop is optional.

# The toolhead

Make a normal Stealthburner toolhead. Print the custom back plate and attach the rail to it.
Insert the magnet holders and keep them loose for now.

It helps to dremel the rail end round to help with alignment:
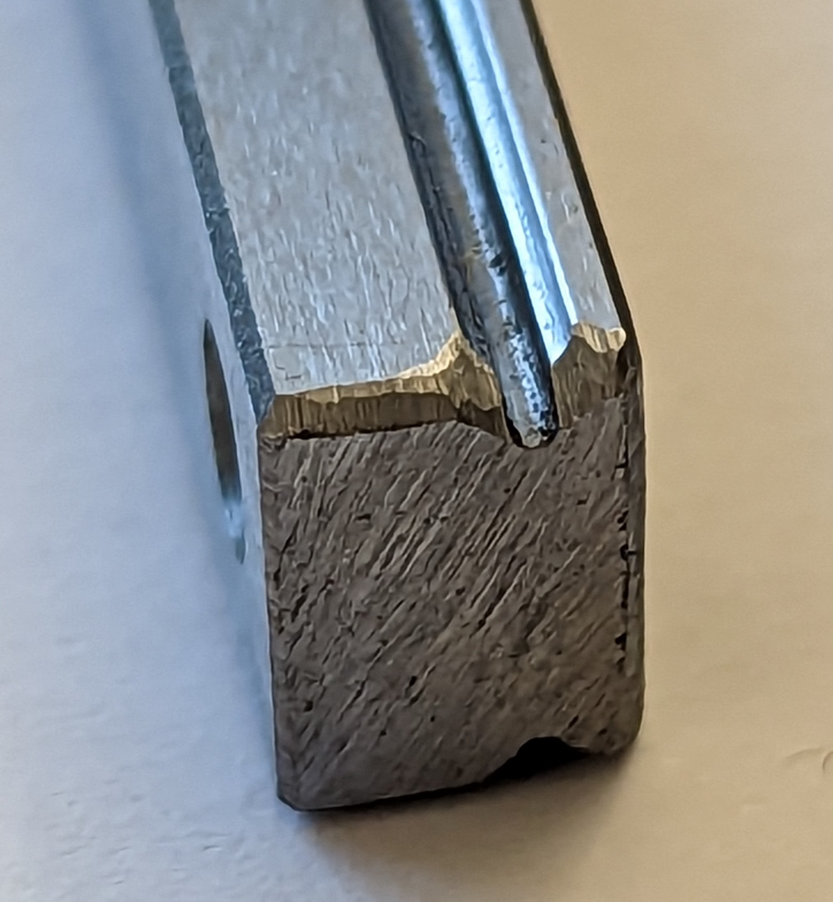
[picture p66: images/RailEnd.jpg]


The final assmeblt looks like this:
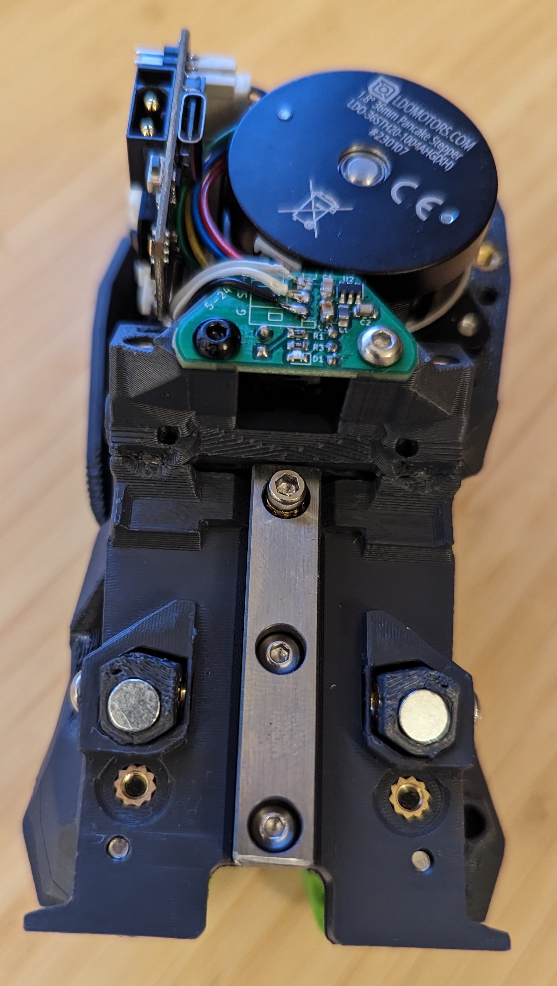
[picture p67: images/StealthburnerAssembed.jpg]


# The dock

Print the parts. 

Press fit a magnet into the pivot.
Attach it to the dock using m3x12 with thread removed from the tips.

Insert a heatset insert into the ozze pad. Then fill the rest with a high temp silicone and let it cure. Screw into place with an m3x8, add a small piece of spring under it to allow some adjustment.

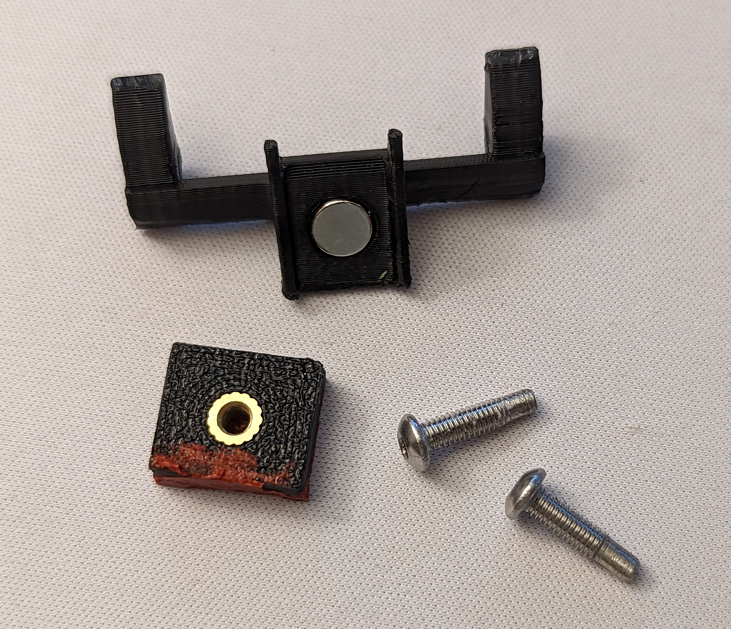
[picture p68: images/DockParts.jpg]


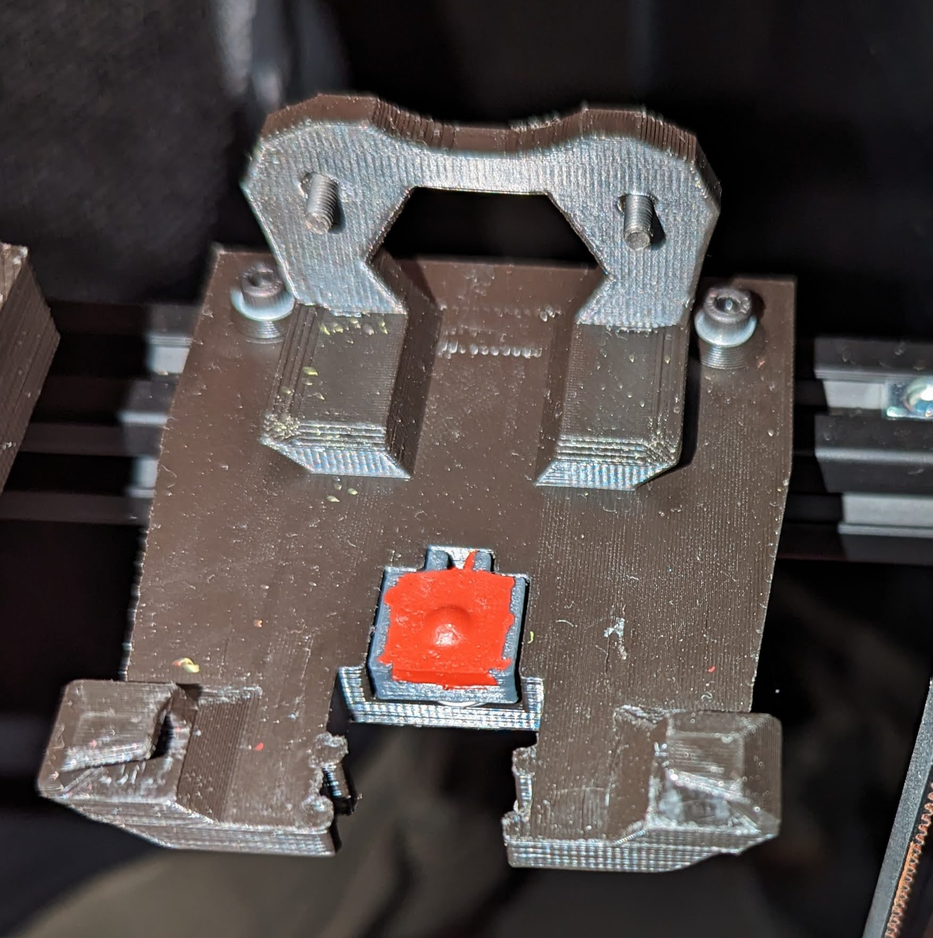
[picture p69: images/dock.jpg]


# The wiring and distribition box

Print & mount the distribution box.
For each hotent print the strain reliefs and 6 clips in TPU.
Wire it all up.

The hotend strain relief is still WIP...

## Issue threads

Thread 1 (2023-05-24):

Canbus setup and wiring

sgermain06, 2023-05-24:
Hi! Thank you for such an amazing project! I'm really looking forward to being done printing it and start installing it on my Voron 2.4! I just have a question regarding the canbus wiring. Which main board are you using and how did you wire up your canbus to support multiple printheads?

Thanks!

AugieSpear, 2023-05-24:
Hi, I have setup the fly sb2040 canbus board and used the fly u2c to connect it directly to the rpi. Im pretty sure you can daisy chain the data signals and end off the chain with a 120 ohm resistor (usually a jumper on the canbus board).

sgermain06, 2023-05-24:
Ah, that makes sense. That means, I could split off the positive and
negative, but connect D+ and D- between the multiple devices in serial,
like RPI -> device 1 D+, device 1 D- -> device 2 D+, device 2 D- -> RPI?

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

viesturz, 2023-05-24:
Can bus is a bus, so all d+ and d- are connected in parallel along the main bus wire.
The toolchanger setup is essentially a star formation, which is poorly supports by Canbus.
But runs fine on 500kbs speed and getting around 10% bus utilization with 3 toolheads.
The Canbus specs has wire length limitations depending on configured speed.
https://community.nxp.com/t5/LPC-Microcontrollers/CAN-FD-wire-length/m-p/1063937
For star layout look at max stub length and accumulated stub length.

I have all the hotend wires connected in parallel inside the filter box at the back and then a beefy power cable going down to PSU. And 120 ohm terminators at USB to can adapter down at the base plus another one in tool 0.

I'm using a canable USB to can board, but have had good success with the Chinese boards as well.
Big tree tech M8P built-in USB to can was unreliable for me though. I suspect mainly because it makes the main board a can node as well and has a lot of traffic to drive all the motors and fans.

sgermain06, 2023-05-24:
Yeah, I'm planning on using the RJ-11 on the BTT Octopus board. Thanks for the information!

Closed 2023-06-28.

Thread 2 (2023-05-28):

Discussion on some issues encountered during the build

EiNSTeiN-, 2023-05-28:
Hi! I just had my first successful load/unload, so first of all thank you for this amazing project!

I'm opening this github issue to discuss some of the pain points I had while they are fresh in my memory hoping this information may be useful to someone else. I'm more than willing to open pull requests to add documentation or modify parts to fix these issues, but I wanted to get some eyes on them first, in case any of them are due to me doing something wrong!

1) I had some parts break due to printing in the wrong orientation, for example the strain relief that goes on the StealthBurner. It would be useful to get them oriented correctly when exporting!
2) Front plate: The holes for the the inserts under the rail are not long enough, the plastic pools at the back and pushes against the inserts, preventing them from sitting flush with the top of the plastic part.
3) Tap PCB: The sensing zone on my optical sensor was too far back to sense the shuttle arm being inserted. I had to add two washers between the PCB and the plastic part to move the sensor forward a bit. Unfortunately I got the PCB from another user on the voron discord so no idea of the origin, whether it's just this one model or a widespread issue.
4) Shuttle: I got pan head screws from McMaster, they fit in the shuttle holes very snug and were impossible to actually turn. I ended up drilling the holes with a flat endmill but some additional clearance would be good.
5) Shuttle: Making it 3mm thicker to recess the carriage screws more would make it possible to use BHCS screws with a ball end allen key, I think that would be more convenient than the flat head screws! I got a box of 100 but don't see myself using the rest of them for anything... With the added extrusion adding 20mm at the front of the printer, I think some added thickness to the shuttle would work just fine.
6) Belts: I originally tie-wrapped the belts but didn't insert them in the little plastic loops on the side of the shuttle, but that causes interference while loading/unloading. I suspect I'm not the only one who will cut corners on this...
7) Dock: I broke the front part where screws catch on the magnets while installing! It needs ridges at 90 degrees at the back to make that bit stronger.
8) Dock: I used 3x18mm dowel pins which removes the need to use a dremel and modify some screws. I used a 3mm reamer on the dock for friction fit and a 1/8" drill on the hinged part for a loose fit. I think this step will be a source of variability from build to build so using an off the shelf part instead of a hand-made part would be really nice.
9) Dock: Broke multiple of them while inserting the magnet in the hinge, a little bit more clearance or a break tab designed into the part would be great.
10) How do you hold the magnets at the front of the SB? The 5mm magnets are too small, and the 6mm ones are too big. I ended up reaming the holes to 6mm and inserted a magnet with a really good friction fit. However it'll be impossible to remove them without breaking the SB cover :( For now I left the magnets out and I can load/unload the tool just fine. but I can see the magnets would help stabilize the toolhead.
11) The config seems to break the regular behavior of M104/M109, the commands just don't have any effect unless there is an active tool, which isn't the case unless `pickup_gcode` runs once (the `M568` line is what sets the active tool), so right after starting the printer there is no active tool and temperature gcodes don't have any effect. I lost a bit of time figuring that one out, I think adding `M568 P{printer.tool_probe_endstop.active_tool_number} A2` to `check_active_tool_on_startup` might be an appropriate fix for this?

Other small details worth adding to the documentation somewhere
* Would be great to specify the location of the extrusion onto which the docks are attached in relation to your printer frame. For example I attached mine with 150mm spacing between the two extrusions, and the first dock is attached 30mm to the left of the frame. I mention this because I crashed my gantry due to wrong dock positioning!
* `position_min` must be adjusted for Y to `-10` to reach the dock, and must make sure the gantry allows for that movement!
* `position_max` should be adjusted for Z to 340, I believe the default is 310 (that's what mine was set to)

viesturz, 2023-05-28:
Thanks for this!
A lot of super useful info, will work though them one by one.

It would be useful of you can split this out into multiple bugs - general
printed parts fit; design ideas; configuration, etc.

Also some pictures would be very appreciated.

One note: I'm printing all this stuff with outer layer first which leads to
better tolerances and slight bias towards undersized parts.

Some initial replies:

1: any good tools to do that? Fusion360 seems overkill to
load-rotate-export.

2: yes this is a tradeoff between extra Y distance and installation
convenience. I'm just trimming off the extra with a hobby knife. Will
experiment with this some more.

3: my PCBs work just fine. The pcb alignment is exactly the same as in
regular Tap. Suspecting your part is off.

4: can you please post the diameter of your screws?

5: cool idea! Can you make a test jig and figure out how many mm is a good
distance?
I might get around to it at some point, but that would speed things up.

6: yeah good point, updating the instructions.

7: never have broken it. But I did made it thinner on last update to add a
bit more flex for more Y tolerance.

8,9: I'm considering of the pivoting part is useful at all. Might be more a
finicky distraction than good.

10: I use black steel bolts and 5mm magnets - they are just magnetically
sticking to the bolt heads.

11: if you can describe your SW setup a bit more?
The gcode macros are copied from TypQxQ repo. Plus an extra delayed macro
to detect the currently mounted tool at boot time. Maybe that one is not
working for you?

Cheers!
Viesturs

On Sun, May 28, 2023, 18:51 Francois Chagnon ***@***.***>
wrote:

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

EiNSTeiN-, 2023-05-30:
I'll split this issue up into new ones :+1:

EiNSTeiN-, 2023-06-10:
I think all these are addressed

Closed 2023-06-10.

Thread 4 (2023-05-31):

STL files orientation

EiNSTeiN-, 2023-05-31:
As I noted in https://github.com/viesturz/tapchanger/issues/2 some STL files are exported in the wrong orientation, I had broken parts due to printing the shuttle and the strain relief adapter incorrectly (printed upright rather than flat on the bed).

I did some research since I'm fairly beginner at fusion 360, one method that was suggested is to create a new document, import each component into it and orient them in relation to the document's Z axis, using the align tool on the face that is supposed to be at the bottom. If you export the STLs from that document, they should be oriented correctly. Since the link will be maintained with the source components you only need to do this once, and just update the source components before exporting.

Alternatively, the way I've been doing it, is re-orienting the parts using slic3r via the command line:
```sh
slic3r --export-stl --ensure-on-bed --repair --output "\[a\] Shuttle.stl" --rotate-x=270 "\[a\]_Shuttle_reoriented.stl"
```
This should work with any of the slic3r-based tools (PrusaSlicer, SuperSlicer, etc)

EiNSTeiN-, 2023-06-10:
looks like 0e32dcc670e342eb68521999f5103bd7880eaf70 fixed this

Closed 2023-06-10.

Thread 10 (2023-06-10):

Improve documentation for adding a new toolhead

EiNSTeiN-, 2023-06-10:
I took some notes while installing my new extruder and cleaned them up here: https://gist.github.com/EiNSTeiN-/0035b747aac1895fe47b7ff0676973ad. I'll keep working on them but hopefully this is useful to someone, since the instructions in `setup.md` are a bit light on details...

I'm opening an issue instead of a pull request because I thought it would be useful to get some eyes on these instructions, I don't know if everything is correct or the easiest way to do everything. I've been following these steps to setup my own extruders successfully so I thought I'd share them to get some feedback.

viesturz, 2023-09-18:
Thanks, this is nice. Will adapt what I can. The entire project has moved away from the rails however.

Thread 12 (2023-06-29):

Add Hall effect magnet holder to shuttle

TheSin-, 2023-06-29:
I'm going to attempt this as soon as I can run Fusion360 again. But I wanted to make a ticket so I remembered and I can check it off.

Once added the shuttle can print on its side and shouldn't require supports anymore.  I will test this theory once I mod the design to have the Hall effect pocket from the original Voron Tap, this should add the X end stop from the original design as well which would then be able to remove the XEndstop files from this project.

Of course this is all just theory ATM and I'll have to get the position perfectly matched and make sure I clear the other parts.

viesturz, 2023-09-18:
Added, see the https://github.com/viesturz/tapchanger/tree/main/STL/Endstops

Closed 2023-09-18.

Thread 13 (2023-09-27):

proprietary cad format

sirus20x6, 2023-09-27:
can we get the cad files as step as well? it would be nice to be able to use freecad to open the files and work on them

viesturz, 2023-09-27:
Hi, will add step files later today.

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

viesturz, 2023-09-27:
Added step files for plates and square rods, the round rods version needs a bit more work - I modified it to make square rods, will get back with that soon.

alfskaar, 2023-10-23:
Can we have step files please.

viesturz, 2023-10-23:
Added, let me know if this works, unfortunately the square and round rods are the same model. I'm looking for a way to add both to the same assembly without too much hacks. Let me know if you need the round rods version.

alfskaar, 2023-10-24:
Thanks. Yes I where thinking absolutely using the "round rods" I have printed the two may parts to get a feel for this. I wondered if the end of the M5 screw can be used. I will have close look and see If can find something that is more common available in my tools.

alfskaar, 2023-10-26:
I wonder it whole have be easier if you made several STEP files as I’m  not really sure with one. ? For AFTERBURNER or Stealthburner

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

viesturz, 2024-02-19:
The cad now has no holes at all, but includes the hole shapes - substract the one you need.

Closed 2024-02-19.

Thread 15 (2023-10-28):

BOM

alfskaar, 2023-10-28:
Update the BOM to reflect that there are
Bearings 3x8x4 or 3x10x4 used depending on rods or pads
And flanged (3x10x4)

Update:
After taking a closer lock at the CAD flange bearings is used on the pad version so depending on which one you are building you may need one of this.
                  mm...
Bearings 3x8x4
Bearings 3x10x4
Bearings 3x10x4 flanged (11.5)

Pinned belt Tapchanger
I have started to modify it since I'm building two double Y gantry Voron 2.4 one small one very big.
Like this. I need to use MG9H to make this work without altering the belt pathway on XY joint's

This should make it easier to take the belt on and off and get it at the exact same place.

Inspired by this video.
https://youtu.be/ZaqttrUeE4I?t=282

viesturz, 2023-11-05:
Hi, Updated the BOMs. It would be best if  you can open a new bug for the Pinned Belt.

Closed 2023-11-05.

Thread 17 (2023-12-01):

New DragonBurner Cowling is missing 2 holes

repraph, 2023-12-01:
nice work.

are the two bottom holes on the new "hook on" dragonburner cowling missing on purpose?

viesturz, 2023-12-01:
Good catch. That one is not updated. At this point I'm not sure if the hook on design is worth it.
I think the magnetic pins can work well with some tweaks.
I'm marking it as experimental for now. IE - feel free to print and test it, but further support is unclear.

Closed 2023-12-01.

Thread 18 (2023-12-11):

DragonBurner Dock Hookon, missing from CAD

alfskaar, 2023-12-11:
Nice if you can add it. As I will modify it to mount to my 2020 RatRig V extrusions. 😊

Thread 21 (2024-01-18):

demo script path issue

Marshalldog, 2024-01-18:
found a bug in the klipper tapchanger gcode (tapchanger demo specifically). I can reliably replicate the danger, see video (sorry file too big for discord): https://photos.app.goo.gl/ArAwiZdWHbvGAvva7

the tapchanger.cfg is stock:
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

the dock location's are correct and were tested with tool alignment test.
it tries to move all axis's simultaneously instead of z first then x then y
I can replicate this consistently

Closed 2024-01-19.

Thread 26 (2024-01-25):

JST-XH connector used on CAN distribution board only supports 3A

esb7, 2024-01-25:
If I'm reading the connector specs right (and reading the right connector specs), the JST-XH connector only supports up to 3A.  For a 24v hotend, that maxes out at 72W.  Ideally you'd derate it a bit, so realistically you'd only want to support ~60W or so.  And that power also needs to drive the toolhead PCB, stepper driver, fans, etc... So the largest hot end you'd likely want to run on that is a good bit less than 60W.  It would depend on the specs of the various components being used.

It may be better to use something like the 4-pin Molex Micro-Fit 3.0mm connector that is used on the U2C and EBB36 (I think).  It appears that supports up to 8.5A which should be plenty for the largest of hotends.

M4dMike, 2024-01-25:
+1 had the exactly same thought.
There are even "advanced" Microfit 3 inserts that support up to 10A.

esb7, 2024-01-26:
I should also add that the connector / wiring that connects back to the power supply needs to support the full load of power if all of the hot ends happen to be heating at once.  In this case, that's 6 x ~100W+ == 600W+ @ 24v == 25A.  The 12awg wire used in the example is probably the right size to use.  For the connector, maybe use JST-XH for the two canbus conductors and then a pcb mount terminal block that can handle 25A+ for the supply power lines.

esb7, 2024-01-27:
One thing that was pointed out to me is that typically a hotend / heater will only pull max power during the initial heat up phase.  Once at temperature, it takes less power to keep it heated.  So if the heat up process for each hot end is staggered during the initial print start routine, the total power needs can be lowered.  However I don't have a good estimate for what the power requirements would be in that case.  Maybe something like a 50% - 100% increase over max power for a single toolhead would be sufficient.

viesturz, 2024-02-10:
Thanks for all the commets. I agree the board is not suitable here. Moving to a Old stuff folder.
Personally I'm using wago clones: https://github.com/viesturz/tapchanger/blob/main/images/umbilical-plate.jpg

Closed 2024-02-10.

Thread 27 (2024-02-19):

Stealthburner Toolhead support for TapSensor is too weak

orotecluc, 2024-02-19:
Hi,
Iam trying the StealthBurner Square Rods version of  Tapchanger/STL/Toolheads/Stealthburner.
But everytime, the mount to where Ihave to put the Tap Sensor, breaks off.
Since I have no Fusion360 experience at all, wouldn't it be possible to give it a more sturdy top wall, in line with the mount on the Voron-Tap?
I know, on Voron Tap, the stup is completly different, with a seperate peace to mount the sensor, and heavy side walls on both sides of the sensor, to make the mount more sturdy, but I think, with a thicker top layer on mount piece, we can have already a good result.
I tried doing a mockup in Tinkercad :
- [https://i.imgur.com/PHsDbpf.png](Zoomin)
- [https://i.imgur.com/Zt0iHWP.png](full view)
I know my 3D drawing skills are close to none

viesturz, 2024-02-19:
Can you add a picture how exactly it breaks off?
Does it break during assembly? Or when printing?

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

orotecluc, 2024-02-19:
It breaks OFF during assembly.

Verzonden vanaf Outlook voor Android<https://aka.ms/AAb9ysg>
________________________________
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

orotecluc, 2024-02-19:
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

The bridge detaches rally easaly, but i thank, if we kake the backpart of that bridge stronger, Luke in my tinkercatd try, everything Will keep hold

viesturz, 2024-02-19:
Thanks, making a more robust version...

viesturz, 2024-02-19:
There, added 2 mm of plastic, let me know if this works.

orotecluc, 2024-02-19:
sorry, late out this evening. Testprinting right now.
Thanks for the fast response

orotecluc, 2024-02-20:
Prints are great now, mounted complete Square-rod-toolhead. Just had some issues mounting the TAP sensor, BHCS6mm are a bit too long, it seems, and screw holes are really narrow. Double magnets are a great upgrade.

Closed 2024-02-19.

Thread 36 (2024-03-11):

OMG... the new DB Cowling design.

walterwissmann, 2024-03-11:
The old one with the markers was a better design and his functionality was very good ;-)

viesturz, 2024-03-11:
Thanks for the input. I agree the new ones are a bit fugly.
Moved away from main branch for now.

So there are two cahnges I'm trying to do with this:
- move the hook points further apart for better docked stability.
- allow for ~1mm tolerance in all directions.

Let me know if you have some ideas how to better get there.

viesturz, 2024-03-11:
I sketched up an alternative. Kinda a middle ground between all form and all function.
Will test print and upload.
Let me know if you have ideas.

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

walterwissmann, 2024-03-11:
The look and feel of the old version with the markers has a high-quality and friendly appearance:

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

Two thinks i have done per hand to have a super functionality:

a. i have make the front holes a little bit grater, 6,5mm.

b. I cut the plastic spacers for the suspension bolts on the park mount a little conically so that the plastic remains behind the bolt and the Dragonburner doesn't bump into it.

This allows the cowling to slide easily over the screw into position.

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

BR
roerich_64

p.s. we can discus via discord. i am also there ;-)

Closed 2024-04-03.

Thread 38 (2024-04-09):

With the support of version 4.0, even Voron Trident compatibility is within reach.

Lukacs5, 2024-04-09:
it can replace the movement of the head's z-direction offset by moving the toolhead motors (liftbar) up and down.

viesturz, 2024-05-20:
Yes, that's the plan. However I do not have a trident myself. So will need someone to step up and try running this on trident.

Closed 2024-05-20.

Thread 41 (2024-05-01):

CAD for the new toolhead

nhchiu, 2024-05-01:
Do you have the CAD file for the new toolhead introduced in V4.1 available?

viesturz, 2024-05-06:
https://github.com/viesturz/tapchanger/blob/main/Tapchanger/CAD/Tapchanger-All.step

viesturz, 2024-05-07:
Added https://github.com/viesturz/tapchanger/blob/main/Tapchanger/STL/Toolheads/DragonBurner/HGX%20Gears/CAD.step

nhchiu, 2024-05-08:
@viesturz If you had taken CAD files from other projects to use in your design,
please note where you took it from properly.

viesturz, 2024-05-08:
See the credits in readme.md
Or let me know if you have specific concerns.

Viesturs

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

nhchiu, 2024-05-08:
@viesturz Did you use the design from here? https://github.com/nhchiu/VoronMods/tree/main/Extruders%2FProtoXtruder

viesturz, 2024-05-08:
Yes, that's right, updated the credits.

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

Closed 2024-05-07.

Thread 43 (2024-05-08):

Beacon Support

gfacek, 2024-05-08:
I just finished my Voron 2.4 a few weeks ago, and since I decided to build it, I've been following this project because I was hoping to replace my old IDEX with it.

Since the Tap Kit from Chaoticlab broke after a short time, and I had been toying with the idea of a Beacon anyway, I swapped the Tap for Beacon (since Beacon can't do CAN, I use Cartographer 3D) and am simply thrilled with how reliably and quickly it works.

So much for the preface.

I'd like to tackle this tool changer next, but I'm wondering how best to implement it with Beacon. I don't think it makes much sense to build a beacon for every toolhead. Hence my thought:
Does it perhaps make sense to add a mount for the beacon to the shuttle? You would then have to pick up each toolhead to be used once at the start of printing in order to calibrate Z.

Would something like that work?

viesturz, 2024-05-20:
I would probably go with adding a beacon to a single toolhead.

Or alternatively add more stuff to shuttle.
I have considered moving the part cooling fans on the shuttle, but the space is really tight.

colin342, 2024-07-08:
Hi

I did setup two tools and one tool has the cartographer3d the other has tap. Now I am struggling to setup the probes part. Once the cartogrpaher is setup and I import the tool_detection.cf, I get the error Duplicate chip name 'probe'. The thing is I kinda understand why, but I have no idea if it can be solved.

gfacek, 2024-07-13:
I'm still waiting for my parts I ordered. But I also think, this is the best solution. So I can "only" have 5 tool for printing, but 1 tool for bed mesh with cartographer.

Do you document your your project anywhere? I'm also interested in helping to design. I'm not very experienced, but can somehow handle with fusion 360 (a bit) 😅

nemesit, 2025-02-03:
ideally the beacon probe could be on the shuttle so all heads could use it.

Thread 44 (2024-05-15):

Shuttle issue below belts

vikwin, 2024-05-15:
I noticed that the non-aluminum shuttle warps a lot when it is attached to the linear rail. When looking for the cause, I saw that the smooth surfaces next to the belts are not in the same plane, but are offset.
I noticed this with the “old” version from before 2024-05-08, but it is also the case with the newer version.
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

Edit:
For the aluminum version, the same seems to apply for the surface between the belts - it's offset to the surfaces below and on top of the belts. That's not the case for the non-aluminum version, which makes me think it hasn't been made that way on purpose. I could be wrong though...

viesturz, 2024-05-16:
Hmm, indeed. Let me try to fix it.
The belt groove profile was imported from previous iteration, perhaps
something is messed up there.

This aside, there should be some deformation from bolting down the shuttle
from the belt compression. You should be able to compensate by adjusting
the bottom screws on each toolhead.

On Wed, May 15, 2024, 22:26 Viktor Winkelmann ***@***.***>
wrote:

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

vikwin, 2024-05-17:
Thanks for your fast reaction, I really appreciate your efforts for the community with tapchanger!
Do you have any plans on removing the central area padding for the aluminum version as well?

viesturz, 2024-05-17:
I added separate keeper optimized versions instead.

On Fri, May 17, 2024 at 3:06 PM Viktor Winkelmann ***@***.***>
wrote:

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

Closed 2024-05-16.

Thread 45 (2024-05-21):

Toolhead 2 and above temperatures cant be controlled through fluidd gui

nateb16, 2024-05-21:
Hi, I've set up my tool changer configurations and encountered an issue I can't resolve. Currently, I can home/dock successfully, control fans, and calibrate tool Z offsets. The problem arises when I try to preheat my toolheads for printing. I have two toolheads set up (T0/extruder and T1/extruder1). Heating T0 through the GUI works fine; Fluidd sends the command `SET_HEATER_TEMPERATURE HEATER=extruder TARGET=115`, and the tool heats up correctly. However, when I try to heat T1 through the GUI, Fluidd sends the command `SET_HEATER_TEMPERATURE HEATER=extruder1 TARGET=115`, and the console responds with `// Heater extruder1 not supported`. Using M104 to set the temperature through G-code works as a temporary workaround, but I feel this needs to be fixed as it breaks a core function of fluidd and makes setting temperatures quickly during a print impractical.

I have attached the console output for reference and my toolhead configs as .txt files for your consideration.

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
[CanBus_T0.txt](https://github.com/viesturz/tapchanger/files/15387737/CanBus_T0.txt)
[CanBus_T1.txt](https://github.com/viesturz/tapchanger/files/15387740/CanBus_T1.txt)

I hope I haven't submitted this ticket prematurely and that a easy fix exists so I can share it with the community since I have noticed this does happen to some people. I thank you for all your hard work and innovation in our community.

nateb16, 2024-05-21:
OK so turns out It was a conflicting macro that I didn't even suspect found at this address.
https://github.com/VoronDesign/VoronUsers/tree/main/printer_mods/Ellis/Bed_Fans

a user in the discord gave me a fix that can be used.
Change
    {% else %}
        {action_respond_info("Heater %s not supported" % HEATER)}
To:
    {% else %}
        _SET_HEATER_TEMPERATURE {rawparams}
Line 52

Closed 2024-05-21.

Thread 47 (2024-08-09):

Need Help...

printicus, 2024-08-09:
Is there anyway to DM you? I need some help in an related project.... thank you.

printicus, 2024-08-13:
Please, I need to do some testing. I need to know what changes do i need to make so I can use normal homing, with watever probes is instaled on the printer. Somethig like when i install the toolchenger extension it should not mess with whatever homing probes are instaled on printer and use them how they are. Thank You.

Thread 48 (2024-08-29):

New Cowling step file.

selkethx, 2024-08-29:
Please, Is it posible upload the last versión cad file of dragon burner cowling? The last cad file is eight month ago and the stl file is two mounth ago. I want add one mod to wire the logo led

Thank you.

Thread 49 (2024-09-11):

Crossbar dragonburner dock and dock mount not compatible

levholt, 2024-09-11:
They do not fit together, seems one of them was changed and not the other.

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

bronsn, 2024-11-07:
Hello, can u link the stl pls, i couldnt find it.

Ty

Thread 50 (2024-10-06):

Parsing Error

pforrmi, 2024-10-06:
Hi. When I'm include the toolchanger.cfg in my printer.cfg I got a parsing error. Is used the 2.4 version

`Klipper reports: ERROR

File contains parsing errors: /home/pi/klipper_config/toolchanger.cfg
	[line  2]: '  t_command_restore_axis:\n'
	[line  3]: '  params_safe_y: 120\n'
	[line  4]: '  params_close_y: 65\n'
	[line  5]: '  params_fast_speed: 10000 \n'
	[line  6]: '  params_path_speed: 600 \n'
	[line  7]: "  params_type = 'rods_mini_hookon'   \n"
	[line  9]: "  params_pads_mini_path: [{'y':9 ,'z':2}, {'y':8, 'z':0}, {'y':0, 'z':0, 'f':0.5},{'y':0, 'z':-5}, {'y':1, 'z':-7}, {'y':3, 'z':-9}, {'y':7,'z':-11}]\n"
	[line 10]: "  params_pads_sb_path: [{'y':9.5 ,'z':8}, {'y':9.5, 'z':2}, {'y':5.5, 'z':0}, {'y':0, 'z':0, 'f':0.5},{'y':0, 'z':-5}, {'y':1, 'z':-7}, {'y':3, 'z':-9}, {'y':7,'z':-11}]\n"
	[line 11]: "  params_rods_mini_path: [{'z':0, 'y':4}, {'z':0, 'y':0, 'f':0.5}, {'z':-6, 'y':0}, {'z':-10, 'y':3}, {'z':-10, 'y':16}]\n"
	[line 12]: "  params_rods_sb_path: [{'y':9.5 ,'z':8}, {'y':9.5, 'z':2}, {'y':5.5, 'z':0}, {'z':0, 'y':0, 'f':0.5}, {'z':-6, 'y':0}, {'z':-10, 'y':3}, {'z':-10, 'y':16}]\n"
	[line 13]: "  params_rods_mini_hookon_path: [{'z':0, 'y':4}, {'z':0, 'y':0, 'f':0.5}, {'z':-7.3, 'y':0}, {'z':-12.3, 'y':3.5}, {'z':-12.3, 'y':16}]\n"
	[line 14]: "  params_rods_xol_path: [{'y':59, 'z':17.5},{'y':5, 'z':17.5},{'y':5, 'z':0.2},{'y':0.5, 'z':0.1},{'z':0, 'y':0, 'f':0.5},{'z':-5, 'y':0},{'z':-6, 'y':3},{'z':-8, 'y':7},{'z':-10, 'y':16}]\n"
	[line 26]: '  initialize_on: first-use\n'
	[line 27]: '  uses_axis: xyz\n'
	[line 28]: '  on_axis_not_homed: home\n'
	[line 29]: '  initialize_gcode:\n'
	[line 30]: '    DETECT_ACTIVE_TOOL_PROBE\n'
	[line 31]: '    _INITIALIZE_FROM_DETECTED_TOOL\n'
	[line 33]: '  before_change_gcode:\n'
	[line 34]: '    {% set tn = "T"+(tool.tool_number|string) %}\n'
	[line 35]: '    {% if printer["gcode_macro " + tn ] %}\n'
	[line 36]: '       SET_GCODE_VARIABLE MACRO={tn} VARIABLE=color VALUE="\'\'"\n'
	[line 37]: '    {% endif %}\n'
	[line 39]: '  after_change_gcode:\n'
	[line 40]: '    {% set tn = "T"+(tool.tool_number|string) %}\n'
	[line 41]: '    {% if printer["gcode_macro " + tn ] %}\n'
	[line 42]: '       SET_GCODE_VARIABLE MACRO={tn} VARIABLE=color VALUE="\'c44\'"\n'
	[line 43]: '    {% endif %}\n'
	[line 46]: '    {% if tool.params_input_shaper_freq_x and tool.params_input_shaper_freq_y %}\n'
	[line 47]: '      {% if tool.params_input_shaper_type_x and tool.params_input_shaper_type_y %}\n'
	[line 48]: '        {% if tool.params_input_shaper_damping_ratio_x and tool.params_input_shaper_damping_ratio_y %}\n'
	[line 49]: '          SET_INPUT_SHAPER SHAPER_FREQ_X={tool.params_input_shaper_freq_x} SHAPER_FREQ_Y={tool.params_input_shaper_freq_y} SHAPER_TYPE_X={tool.params_input_shaper_type_x} SHAPER_TYPE_Y={tool.params_input_shaper_type_y} DAMPING_RATIO_X={tool.params_input_shaper_damping_ratio_x} DAMPING_RATIO_Y={tool.params_input_shaper_damping_ratio_y}\n'
	[line 50]: '        {% else %}\n'
	[line 51]: '          SET_INPUT_SHAPER SHAPER_FREQ_X={tool.params_input_shaper_freq_x} SHAPER_FREQ_Y={tool.params_input_shaper_freq_y} SHAPER_TYPE_X={tool.params_input_shaper_type_x} SHAPER_TYPE_Y={tool.params_input_shaper_type_y} DAMPING_RATIO_X={params_input_shaper_damping_ratio_x} DAMPING_RATIO_Y={params_input_shaper_damping_ratio_y}\n'
	[line 52]: '        {% endif %}\n'
	[line 53]: '      {% else %}\n'
	[line 54]: '        SET_INPUT_SHAPER SHAPER_FREQ_X={tool.params_input_shaper_freq_x} SHAPER_FREQ_Y={tool.params_input_shaper_freq_y} SHAPER_TYPE_X={params_input_shaper_type_x} SHAPER_TYPE_Y={params_input_shaper_type_y} DAMPING_RATIO_X={params_input_shaper_damping_ratio_x} DAMPING_RATIO_Y={params_input_shaper_damping_ratio_y}\n'
	[line 55]: '      {% endif %}\n'
	[line 56]: '    {% else %}\n'
	[line 57]: '      SET_INPUT_SHAPER SHAPER_FREQ_X={params_input_shaper_freq_x} SHAPER_FREQ_Y={params_input_shaper_freq_y} SHAPER_TYPE_X={params_input_shaper_type_x} SHAPER_TYPE_Y={params_input_shaper_type_y} DAMPING_RATIO_X={params_input_shaper_damping_ratio_x} DAMPING_RATIO_Y={params_input_shaper_damping_ratio_y}\n'
	[line 58]: '    {% endif %}\n'
	[line 59]: "    {% if not printer['gcode_macro PRINT_START'].printing %}\n"
	[line 60]: '        STOP_TOOL_PROBE_CRASH_DETECTION\n'
	[line 61]: '    {% endif %}\n'
	[line 63]: '  dropoff_gcode:\n'
	[line 64]: '    {% set x = tool.params_park_x|float %}\n'
	[line 65]: '    {% set y = tool.params_park_y|float %}\n'
	[line 66]: '    {% set z = tool.params_park_z|float %}\n'
	[line 67]: '    {% set fast = tool.params_fast_speed|float %}\n'
	[line 68]: "    {% set path = tool['params_' ~ tool.params_type ~ '_path'] %}\n"
	[line 69]: '    {% set max_z = printer.configfile.config["stepper_z"]["position_max"]|float %}\n'
	[line 70]: '    {% set cur_z = printer.toolhead.position[2]|float %}\n'
	[line 71]: "    RESPOND TYPE=echo MSG='Dropping off {tool.name}'\n"
	[line 72]: '    STOP_TOOL_PROBE_CRASH_DETECTION\n'
	[line 73]: '    G90\n'
	[line 74]: '    ; Move 1 mm up to avoid crashing into things\n'
	[line 75]: '    G0 Z{ [cur_z+1.0, max_z]|min } F{fast}\n'
	[line 77]: '    ROUNDED_G0 Y={tool.params_safe_y} D=20 F={fast}\n'
	[line 78]: '    ROUNDED_G0 X={x} D=150 F={fast}\n'
	[line 79]: "    ROUNDED_G0 Z={z + path[0]['z']|float} D=20 F={fast}\n"
	[line 80]: "    ROUNDED_G0 Y={y + path[0]['y']|float} D=0 F={fast}\n"
	[line 82]: '    {% for pos in path %}\n'
	[line 83]: "        G0 Y{y + pos['y']|float} Z{z + pos['z']|float} F{tool.params_path_speed|float * (pos.get('f', 1.0)|float) }\n"
	[line 84]: '    {% endfor %}\n'
	[line 86]: '  pickup_gcode:\n'
	[line 87]: '    {% set x = tool.params_park_x|float %}\n'
	[line 88]: '    {% set y = tool.params_park_y|float %}\n'
	[line 89]: '    {% set z = tool.params_park_z|float %}\n'
	[line 90]: '    {% set fast = tool.params_fast_speed|float %}\n'
	[line 91]: "    {% set path = tool['params_' ~ tool.params_type ~ '_path'] %}\n"
	[line 92]: "    RESPOND TYPE=echo MSG='Picking up {tool.name}'\n"
	[line 93]: '    G90\n'
	[line 95]: '    ROUNDED_G0 Y={tool.params_close_y} F={fast} D=5\n'
	[line 96]: "    ROUNDED_G0 X={x} Z={z + path[-1]['z']|float} F={fast} D=5\n"
	[line 97]: "    ROUNDED_G0 Y={y + path[-1]['y']|float} F={fast} D=0\n"
	[line 100]: '    {% if tool.extruder %}\n'
	[line 101]: '      TEMPERATURE_WAIT SENSOR={printer.toolhead.extruder} MINIMUM={printer[tool.extruder].target}\n'
	[line 102]: '    {% endif %}\n'
	[line 105]: '    {% for pos in path|reverse %}\n'
	[line 106]: "      G0 Y{y + pos['y']|float} Z{z + pos['z']|float} F{tool.params_path_speed|float * (pos.get('f', 1.0)|float) }\n"
	[line 107]: "      {% if 'f' in pos %} \n"
	[line 108]: '        M400 ; Wait for moves to finish\n'
	[line 109]: '        START_TOOL_PROBE_CRASH_DETECTION T={tool.tool_number}\n'
	[line 110]: '      {% endif %}\n'
	[line 111]: '    {% endfor %}\n'
	[line 113]: '    ROUNDED_G0 Y={tool.params_safe_y} F={fast} D=20\n'
	[line 114]: "    {% if 'Z' in restore_position %}\n"
	[line 115]: '      ROUNDED_G0 Z={restore_position.Z} F={fast} D=150\n'
	[line 116]: '    {% endif %}\n'
	[line 117]: "    {% if 'X' in restore_position %}\n"
	[line 118]: '      ROUNDED_G0 X={restore_position.X} F={fast} D=1000\n'
	[line 119]: '    {% endif %}\n'
	[line 120]: "    {% if 'Y' in restore_position %}\n"
	[line 121]: '      ROUNDED_G0 Y={restore_position.Y} F={fast} D=0\n'
	[line 122]: '    {% endif %}\n'
	[line 123]: '    ROUNDED_G0 D=0\n'

Once the underlying issue is corrected, use the "RESTART"
command to reload the config and restart the host software.
Printer is halted`

CombatVolcano, 2024-11-10:
I get a set_input_shaper error when trying to switch toolheads, I don't have one configured

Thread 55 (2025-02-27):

If the parameter params_park_z is not needed, how to solve it

angelassie, 2025-02-27:
I'm trying to use a new dock on trident, using a limit slider to separate the shuttle and toolhead, so I don't need 'params_park_z'. But if I don't define this parameter, I get an error when I run tool change. Can you give me a solution?Thanks!

angelassie, 2025-02-27:
> I'm trying to use a new dock on trident, using a limit slider to separate the shuttle and toolhead, so I don't need 'params_park_z'. But if I don't define this parameter, I get an error when I run tool change. Can you give me a solution?Thanks!

When running TOOL_DROPOFF, the toolhead only moves horizontally.

Closed 2025-03-03.

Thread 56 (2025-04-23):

Klipper 13 compliant

metzenw, 2025-04-23:
A recent commit in Klipper broke the tapchanger plugin solution. Folks have been reporting that downgrading to Klipper 12 works around these changes.

Based on that conversation, it seems like the plugin should be updated to be Klipper 13 compliant.

https://klipper.discourse.group/t/stealthchanger-tapchanger-tool-error/23097
https://github.com/Klipper3d/klipper/pull/6879
https://www.reddit.com/r/VORONDesign/comments/1k3y11z/stealthchanger_tapchanger_tool_error/
https://imgur.com/6dxZewl

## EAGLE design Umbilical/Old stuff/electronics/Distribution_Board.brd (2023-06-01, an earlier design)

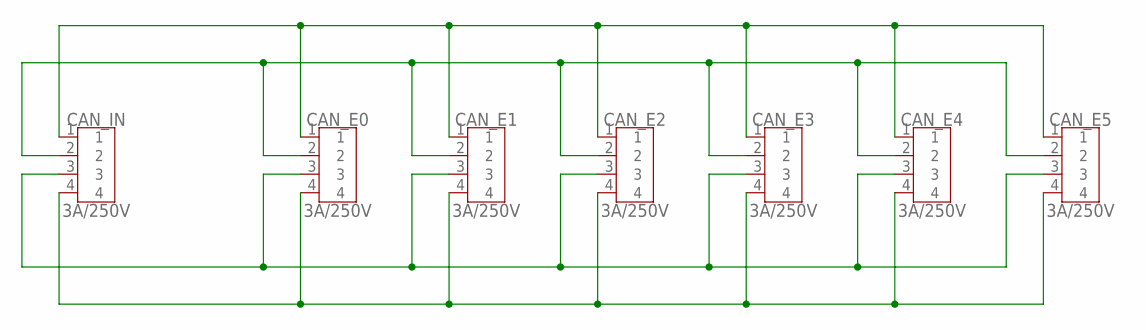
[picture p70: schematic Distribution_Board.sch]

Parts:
CAN_E0, CAN_E1, CAN_E2, CAN_E3, CAN_E4, CAN_E5: 3A/250V; B4B-XH-A
CAN_IN: 3A/250V; B4B-XH-A

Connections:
unnamed: CAN_E0.1, CAN_E1.1, CAN_E2.1, CAN_E3.1, CAN_E4.1, CAN_E5.1, CAN_IN.1
unnamed: CAN_E0.2, CAN_E1.2, CAN_E2.2, CAN_E3.2, CAN_E4.2, CAN_E5.2, CAN_IN.2
unnamed: CAN_E0.4, CAN_E1.4, CAN_E2.4, CAN_E3.4, CAN_E4.4, CAN_E5.4, CAN_IN.4
unnamed: CAN_E0.3, CAN_E1.3, CAN_E2.3, CAN_E3.3, CAN_E4.3, CAN_E5.3, CAN_IN.3

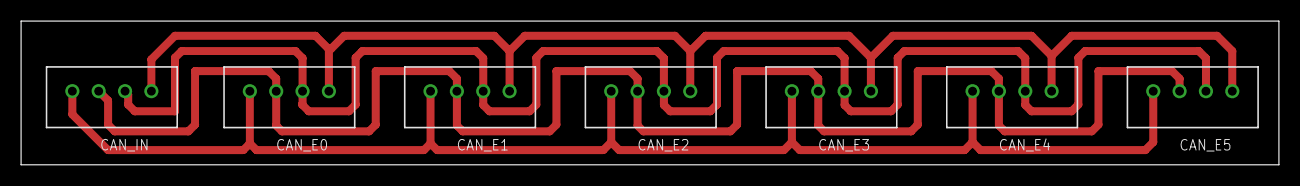
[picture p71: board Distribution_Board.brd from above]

Board: 2 copper layers, 119.4 x 13.6 mm, 7 parts (0 on the bottom side), 4 nets.

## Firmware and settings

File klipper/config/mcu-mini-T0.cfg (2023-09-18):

# This file contains common pin mappings for the BIGTREETECH EBBCan
# Canbus board. To use this config, the firmware should be compiled for the
# STM32G0B1 with "8 MHz crystal" and "USB (on PA11/PA12)" or "CAN bus (on PB0/PB1)".
# The "EBB Can" micro-controller will be used to control the components on the nozzle.

# See docs/Config_Reference.md for a description of parameters.

[mcu et0]
#canbus_uuid: bafd9b10a1b4
canbus_uuid:1a3c230191ed

[temperature_sensor MCU_T0]
sensor_type: temperature_mcu
sensor_mcu: et0


[extruder]
step_pin: et0:PD0
dir_pin: et0:PD1
enable_pin: !et0:PD2
microsteps: 16
rotation_distance: 53.58  # Bondtech LGX Drive Gears
gear_ratio: 44:10, 37:17  # Lgx lite
nozzle_diameter: 0.400
filament_diameter: 1.750
heater_pin: et0:PB13
sensor_type: ATC Semitec 104NT-4-R025H42G
sensor_pin: et0:PA3
control: pid
pid_Kp=21.499
pid_Ki=1.078
pid_Kd=107.228
min_temp: 0
max_temp: 300
min_extrude_temp: 180
pressure_advance: 0.035                                               # See tuning pressure advance doc
pressure_advance_smooth_time: 0.040


[tmc2209 extruder]
uart_pin: et0:PA15
run_current: 0.650
hold_current: 0.1
driver_TPOWERDOWN: 20
stealthchop_threshold: 999999

[multi_fan T0_partfan]
pin: et0:PA0

[heater_fan T0_hotend_fan]
pin: et0:PA1
heater: extruder
heater_temp: 50.0


[adxl345]
cs_pin: et0:PB12
spi_software_sclk_pin: et0:PB10
spi_software_mosi_pin: et0:PB11
spi_software_miso_pin: et0:PB2
axes_map: x,z,y

[tool T0]
 tool_number: 0
 extruder: extruder
 fan: multi_fan T0_partfan
 gcode_x_offset: 0
 gcode_y_offset: 0
 gcode_z_offset: 0
 params_park_x: 138.2
 params_park_y: -7.0
 params_park_z: 305.0
 params_type: 'rods-mini'
 
[tool_probe T0]
pin: !et0:PB6
tool: 0
z_offset: -1.055
speed: 5.0
samples: 3
samples_result: median
sample_retract_dist: 2.0
samples_tolerance: 0.02
samples_tolerance_retries: 3
activate_gcode:
    TAP_PROBE_ACTIVATE HEATER=extruder

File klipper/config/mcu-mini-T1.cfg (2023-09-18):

# This file contains common pin mappings for the BIGTREETECH EBBCan
# Canbus board. To use this config, the firmware should be compiled for the
# STM32G0B1 with "8 MHz crystal" and "USB (on PA11/PA12)" or "CAN bus (on PB0/PB1)".
# The "EBB Can" micro-controller will be used to control the components on the nozzle.

# See docs/Config_Reference.md for a description of parameters.

[mcu et1]
canbus_uuid: 296c6b0da245

[temperature_sensor MCU_T1]
sensor_type: temperature_mcu
sensor_mcu: et1

[extruder1]
step_pin: et1:PD0
dir_pin: et1:PD1
enable_pin: !et1:PD2
microsteps: 16
rotation_distance: 34.433 # 34.777
gear_ratio: 7.5:1                                                   # For Orbiter V2
nozzle_diameter: 0.400
filament_diameter: 1.750
heater_pin: et1:PB13
sensor_type: ATC Semitec 104NT-4-R025H42G
sensor_pin: et1:PA3
control: pid
pid_Kp=32.340 
pid_Ki=4.312 
pid_Kd=60.639
min_temp: 0
max_temp: 300
min_extrude_temp: 180
pressure_advance: 0.035                                               # See tuning pressure advance doc
pressure_advance_smooth_time: 0.040


[tmc2209 extruder1]
uart_pin: et1:PA15
run_current: 0.650
hold_current: 0.1
driver_TPOWERDOWN: 20
stealthchop_threshold: 999999

[multi_fan T1_partfan]
pin: et1:PA0

[heater_fan T1_hotend_fan]
pin: et1:PA1
heater: extruder1
heater_temp: 50.0


# [adxl345]
# cs_pin: et1:PB12
# spi_software_sclk_pin: et1:PB10
# spi_software_mosi_pin: et1:PB11
# spi_software_miso_pin: et1:PB2
# axes_map: z,-y,x


[tool T1]
 tool_number: 1
 extruder: extruder1
 fan: multi_fan T1_partfan
 gcode_x_offset: -0.02
 gcode_y_offset: 0.44
 gcode_z_offset: 0.54
 params_park_x: 273.52
 params_park_y: -6.87
 params_park_z: 305.4
 params_type: 'rods-mini'

[tool_probe T1]
pin: et1:PB6
tool: 1
z_offset: -0.55
speed: 5.0
samples: 3
samples_result: median
sample_retract_dist: 2.0
samples_tolerance: 0.01
samples_tolerance_retries: 3
activate_gcode:
    TAP_PROBE_ACTIVATE HEATER=extruder1

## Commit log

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2023-03-27 Dock change. Add wipe pad.
    [DockBack.stl, DockBase.stl, DockFront.stl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]
2023-03-28 New tip pad design
    [DockBack.stl, DockBase.stl, DockFront.stl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]
2023-03-30 Dock tweaks. Initial cable strain relief.
    [DockBack.stl, DockBase.stl, DockNozzlePad.stl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]
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2023-04-06 Update strain relief, some folders.
    [DockBack.stl, DockBase.stl, DockFront.stl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]
2023-04-06 Distribution box first iteration.
    [Distribution_box.stl, Exhaust_cover.stl, [a]_exhaust_filter_mount_x2.stl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]
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2023-04-07 Tweaks to distribution box and adding a simple clip.
    [[tpu] Clip.stl_x6.stl, [tpu] Strain_relief.stl]
2023-04-07 Let's call it a 0.1
    [[tpu] CableFlex.stl, [tpu] Clip.stl_x6.stl, [tpu] Strain_relief.stl]
2023-04-08 Actual mounting solution. Updated dock to match.
    [DockBack.stl, DockBase.stl, DockFront-SupportsNeeded.stl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]
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2023-04-21 V0.2 First toolchanges confirmed.
    [BeamMount.stl, CalibrationPin.stl, DockBack.stl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]
2023-04-23 Update tool probe code. Quad gantry level works again.
    [Boop-dock.stl, DockBase.stl]
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2023-04-23 Fix z offset to work with homing.
    [DockBase.stl, DockPivot.stl]
2023-04-23 Homing now accounts for current tool Z offset.
    [homing.cfg, macros.cfg, mcu-extruder0.cfg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]
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2023-04-26 Config fix
    [tools.cfg]
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2023-05-08 Remove unnecesaary stuff from dock
    [Boop-dock.stl, DockBase.stl]
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2023-05-31 Add distribution board PCB
    [DistributionBoard.f3d, Distribution_Board.brd, Distribution_Board.sch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]
2023-05-31 Fix typo in canbus
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2023-06-02 Add 3.4mm thickness to the shuttle
    [[a] Shuttle-Lowered3mm-flathead.stl, [a] Shuttle-Lowered3mm.stl, [a] XEndstop-flathead.stl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]
2023-06-03 Add 8mm BHCS Shuttle option
    [[a] Shuttle-Lowered3mm-flathead.stl, [a] Shuttle-Lowered3mm.stl, [a] Shuttle.stl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]
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2023-06-04 Split dock to allow swapping upper part
    [DockBase.stl, DockBase_Lower.stl, DockBase_Upper.stl]
2023-06-04 Split distribution box to make wiring easier
    [Distribution_box-Curved-Body.stl, Distribution_box-Curved-Cover.stl]
2023-06-04 Add 5.6mm CableFlex part
    [[tpu] CableFlex-4.5mm.stl, [tpu] CableFlex-5.6mm.stl, [tpu] CableFlex.stl]
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2023-06-09 Mov rev2 to separate repo
    [Mount-MiniSB.stl, Shuttle.stl, XEndstop.stl]
2023-06-10 Rotate stls to correct print orientation
    [BeamMount.stl, Distribution_box-Curved.stl, Distribution_box.stl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]
2023-06-11 Klipper update. Fixing some tools calibrate bugs.
    [calibrate-offsets.cfg, printer.cfg, tools_macros.cfg]
2023-06-16 Make the tool config ~sane; TCLite support in config. Basic Z offset description.
    [calibrate-offsets.cfg, homing.cfg, macros.cfg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]
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2023-06-18 Fix orientation
    [BowdenTubeOragnizer.stl]
2023-06-25 Fixes to bowden tube organizer
    [BowdenTubeOragnizer.stl]
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2023-09-23 Slightly righten the square rods slot, reduce screw angle from 0.5 to 0.2 deg
    [Mount-square-rods.stl]
2023-09-27 Update calibrate offsets script to output savable config changes.
    [calibrate-offsets.cfg]
2023-09-27 Update example config. Some cleanups after setting up all 6 tools. And wait for tool to come to temp before picking it up from dock.
    [T0-sb-rapido.cfg, T1-mini-revo.cfg, T2-mini-revo.cfg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]
2023-09-29 Tweaks to example config. Remove config for legacy toolchanger.
    [homing.cfg, macros.cfg, toolchanger.cfg]
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2023-10-02 Dragon burner test plate
    [[dev] Mount.stl]
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2023-10-07 Dragon burner dev
    [Cowling.stl, [dev] Dock.stl, [dev] Mount.stl]
2023-10-08 Dragon burner adapter v1
    [Dock.stl, Mount.stl, PadClip.stl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]
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2023-10-13 Enhancements to add Shuttle Keeper and Rear X Endstop Mount
    [Rear X Endstop Mount.stl, Rear-X-Endstop-Mount.step, Shutlle-Keeper.step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]
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2023-10-29 Small tweaks to all square rods - looser fit and more accurate adjustment screw angle.
    [10x4 PlateCuttingJig1.stl, 10x4 PlateCuttingJig2.stl, 10x5mm rod jigA.stl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]
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2023-11-27 Move all the klipper extensions to a single repo.
    [Cowling.stl, Default Cowling.stl, DragonBurner Dock-V2.stl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]
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2023-12-08 Redo the hook on dock. Make the Dragon cowling universal.
    [Cowling.stl, DragonBurner Cowling.stl, DragonBurner Dock - Hook on.stl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]
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2023-12-09 Updated config example. With support for hook on docking.
    [T0-dragon.cfg, T1-dragon-revo.cfg, T2-dragon-revo.cfg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]
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2023-12-15 Add more clearance for shuttle middle legs to exit.
    [Mount Round Rods.stl, Mount Square Rods.stl]
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2023-12-17 Macros updates
    * preheat all hotends in use
    * fix wait for hotend temp before undocking the tool.
    * larger max radius for docking approach/depart.
    [macros.cfg, toolchanger.cfg]
2023-12-21 Minor cleanups all across.
    - [All] better tensioning screw angle
    - [Dragon] migrate to DragonBurnerV8
    - [Dragon] move the ventilation gap next to the hotend to minimize heat transfer to the mount.
    - [All] fixed missing gap between OptoTap and the shuttle.
    - [All] slightly move OptoTap scew holes back
    [Cowling.stl, DockMount.stl, DragonBurner Dock - Hook on - screw length reference.stl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]
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2023-12-23 Dragon burner mount plate: Trim off some material.
    [Mount Round Rods.stl, Mount Square Rods.stl]
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2023-12-29 Add files via upload
    Improved rigidity (may have issues with led install)
    [Rapid Burner Cowl.stl]
2023-12-29 Add files via upload
    adds tool head latch mechanism from Dragon Burner
    [Rapid Burner Cowl.stl]
2023-12-29 Add files via upload
    clean up on the design
    [Rapid Burner Cowl.stl]
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2024-01-19 add tapchanger-rods xol-toolhead dock, maglock faceplate and base
    add tapchanger-rods xol-toolhead dock, maglock faceplate and base (experimental, only for tapchanger-(lite)-rods)
    [Tapchanger-Lite-Rods-Base-Xol-Toolhead.step, Tapchanger-Lite-Rods-Xol-Toolhead_Dock.step, Tapchanger-Lite-Rods-Xol-Toolhead_MaglockFaceplate.step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]
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2024-02-05 Brace + Idlers update
    More clearance and endstop slot.
    [Brace-Left.stl, Brace-Right.stl, Idler-Top Left.stl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]
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2024-02-06 Fix brace slide width to 6.2mm.
    [Brace-Left.stl, Brace-Right.stl]
2024-02-10 add input shaper type to example toolchanger.cfg, T0.cfg, T1.cfg
    changes to example toolchanger.cfg, T0.cfg, T1.cfg
    add add support for input shaper type to tools. defaults to params in toolchanger.cfg if shaper params are not set in tool.
    [T0-burner-dragon.cfg, T1-mini-revo.cfg, toolchanger.cfg]
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2024-02-10 Remove distribution board, this is not suitable for the amps it will be pulling.
    [Distribution_Board.brd, Distribution_Board.sch, Distribution_Board_v6.f3z]
2024-02-17 add shaper damping ratio as optional tool param
    add shaper damping ratio as optional tool param
    [T0-burner-dragon.cfg, printer.cfg, toolchanger.cfg]
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2024-03-09 DragonBurner dock redesign - way more alignment clearance.
    [Cowling.stl, DragonBurder Dock.stl, DragonBurder DockMount.stl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]
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2024-03-11 Revert "DragonBurner dock redesign - way more alignment clearance."
    This reverts commit b80ea15ed5b037be775f1505a19a4ce3a0c08461.
    [Cowling.stl, DockMount.stl, DragonBurder Dock.stl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]
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2024-03-17 Dragonburner - Updated hook interface.
    Provides room for about 1mm offset in XZ.
    [Cowling.stl, DragonBurder Dock.stl, DragonBurner Dock.stl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]
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2024-03-30 Dragon Burner dock tweaks.
    [Cowling.stl, DragonBurner - Dock.stl, DragonBurner Dock.stl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]
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2024-04-02 More clearance at the dock legs.
    [DragonBurner - Dock.stl, DragonBurner.stl]
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2024-04-21 Dragon burner - Landing new cowling & dock.
    [Cowling.stl, DragonBurner - Dock.stl, DragonBurner Dock Hook on.stl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]
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2024-05-08 Fix orientation.
    [Shuttle Rods Dual Magnets.stl, Shuttle-rods-Aluminium.stl, Shuttle-rods-thruholes.stl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]
2024-05-08 Shuttle tweaks
    Move the old stuff away, improve printability a bit. Update the Aluminium model to 2 magnets.
    [MiniSB-Mount-pads.stl, SB-Mount-pads.stl, Shutlle Keeper.stl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]
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2024-05-12 Update Back+5mm.stl
    Fix orientation
    [Back+5mm.stl]
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2024-05-16 Fix shuttle base misalignment.
    Fixes #44
    [Shuttle.stl]
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2024-05-18 Add 1 mm to Dragon Burner back plate - more clearance for the fans and adjustment screws.
    [Back Drive Gear.stl, Mount Round Rods.stl, Mount Square Rods.stl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]
2024-05-19 Add 1mm extra spacing around the motor to accomodate bigger motors.
    [Back+5mm.stl, Back.stl, Front Bambu.stl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]
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2024-05-20 Revert "RapidBurner docks"
    This reverts commit d88aca647cb9b013e654e3f454001fa21dd06c89.
    [RapidBurner - Dock.stl, RapidBurner.stl, RapidDragonBurner.stl]
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2024-05-24 Fix some print orientations.
    [Back+5mm.stl, Backplate.stl, EBB36 Shield.stl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]
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2024-06-16 Dragon burner - Better printability with polycarbonate.
    [Cowling.stl, Mount Round Rods.stl, Mount.stl]
2024-06-28 Small Dragon burner updates.
    [Cowling.stl, Galileo2 Spacer.stl, Mount Round Rods.stl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]
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2024-11-05 Dual loop gantry
    Adding a dual loop gantry with independent motors and endstops.
    [2x Tensioner1.obj, 2x Tensioner1.stl, 2x Tensioner2.obj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]
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
